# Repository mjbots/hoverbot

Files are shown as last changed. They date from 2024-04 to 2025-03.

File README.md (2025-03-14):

mjbots hoverbot
===============

Source and design files for the mjbots hoverbot, its controlling
interfaces, and utilities for developing and operating it.

* GitHub https://github.com/mjbots/hoverbot
* Most files are free hardware and software: Apache 2.0 License
* F360 assembly: https://a360.co/3Fpwtx1
* [BOM](BOM.md)

Directory structure
-------------------

* **base/** - C++ source files common to many applications.
* **mech/** - C++ source files specific to walking robots.
* **utils/** - Utilities for development and data analysis.
* **configs/** - Configuration files for different robots and applications.
* **hw/** - Hardware design files
* **docs/** - Documentation.

First Time Setup
----------------

The following should work on Ubuntu 22.04

```
./install-packages
```

Building for host
-----------------

```
tools/bazel test //...
```

Building for the target
-----------------------

```
tools/bazel test --config=pi //mech:hoverbot_deploy.tar
```

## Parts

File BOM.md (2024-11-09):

# Hoverbot BOM

* 3D printed parts (all designed for Prusament PETG with a Prusa MK3s and 0.6mm nozzle)
  * [Base](hw/hoverbot_base.3mf)
  * [Chassis](hw/hoverbot_chassis.3mf)
  * [Chassis cover](hw/hoverbot_chassis_cover.3mf)
  * [Base cover, battery rails, and battery cover](hw/hoverbot_rails_base_cover.3mf)
* Electronics
  * 2x [moteus-c1](https://mjbots.com/products/moteus-c1)
  * [pi3hat](https://mjbots.com/products/mjbots-pi3hat-r4-5)
  * [power_dist](https://mjbots.com/products/mjbots-power-dist-r4-5b)
  * [Raspberry Pi 4 / 2GB](https://www.raspberrypi.com/products/raspberry-pi-4-model-b/)
  * [64GB Micro SD Card](https://www.amazon.com/gp/product/B09X7C7LL1)
* Connectors and cabling
  * 3x [30cm PH3 cable](https://mjbots.com/products/jst-ph3-cable)
  * 3x XT30 power cables, each with
    * 1x [XT30 Male](https://mjbots.com/products/xt30u-m)
    * 1x [XT30 Female](https://mjbots.com/products/xt30u-f)
    * ~30cm [18 AWG silicone wire](https://www.amazon.com/gp/product/B01KCPL3Z8)
    * heat shrink tubing
  * 2x motor wiring, each with
    * 1x [MR30 connector pairs](https://www.amazon.com/gp/product/B0747MW9RX)
    * 1x [GH7 housings](https://mjbots.com/products/jst-gh7-housing)
    * 5x [GH pre-crimped wires](https://mjbots.com/products/jst-gh-wire)
    * small heat shrink tubing
  * Power cable
    * [XT90S](https://www.amazon.com/gp/product/B0893CGLP7)
    * ~20cm [16 AWG silicone wire](https://www.amazon.com/gp/product/B01MCRY7OT)
* Battery mount
  * 2x [M3x4 bolt / 91292A109](https://www.mcmaster.com/91292A109/)
  * [Battery PCB](hw/battery_pcb/)
  * 2x [Battery Terminal / 1289](https://www.digikey.com/en/products/detail/keystone-electronics/1289)
* Hardware
  * 28x [M3 heat set inserts / 94180A331](https://www.mcmaster.com/94180A331/)
    * 18x in base
    * 10x in chassis
  * 8x [M2.5 heat set inserts / 94180A321](https://www.mcmaster.com/94180A321/)
    * 8x in chassis
  * 16x [M2.5x5 bolts / 91292A009](https://www.mcmaster.com/91292A009/)
    * 8x for moteus-c1
    * 4x for power_dist
    * 4x for pi3hat
  * 26x [M3x8 bolt 91292A112](https://www.mcmaster.com/91292A112/)
    * 8x for motors
    * 4x for base cover
    * 4x for chassis cover
    * 4x for chassis
    * 6x for battery mounts

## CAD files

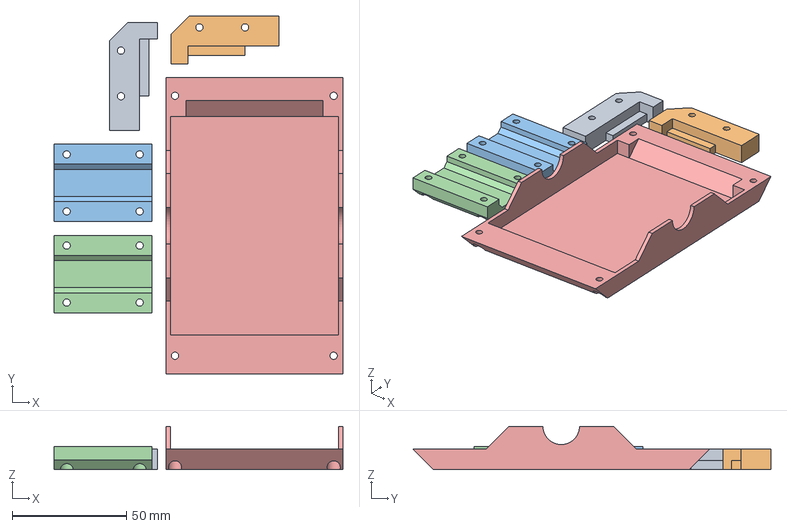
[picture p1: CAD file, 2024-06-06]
hw/hoverbot_rails_base_cover.3mf
126.6 x 157.0 x 19.0 mm
hoverbot_battery_rail2.stl
hoverbot_battery_rail1.stl
hoverbot_motor_mount2.stl
hoverbot_motor_mount1.stl
hoverbot_base_cover.stl

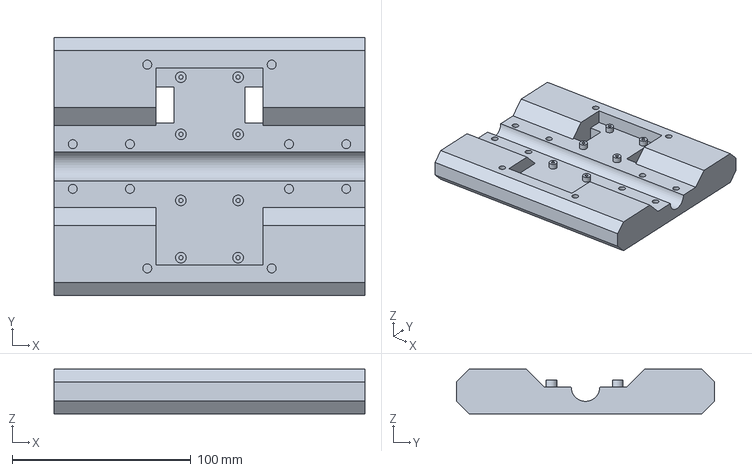
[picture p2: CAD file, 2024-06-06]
hw/hoverbot_base.3mf
174.0 x 144.1 x 25.0 mm

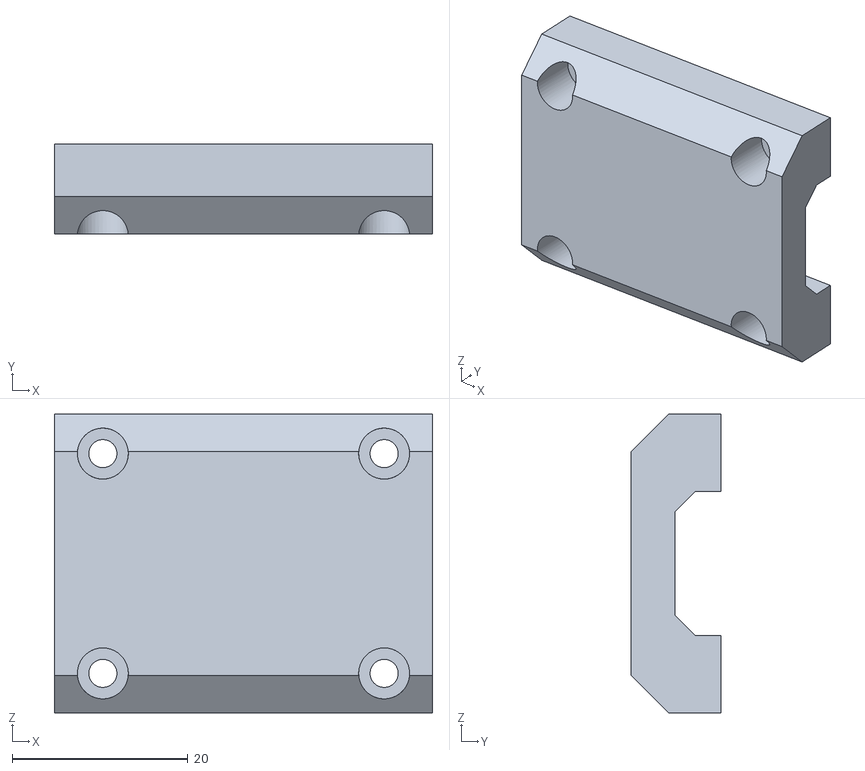
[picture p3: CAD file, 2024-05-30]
hw/hoverbot_motor_mount1.stl
43.0 x 10.2 x 34.0

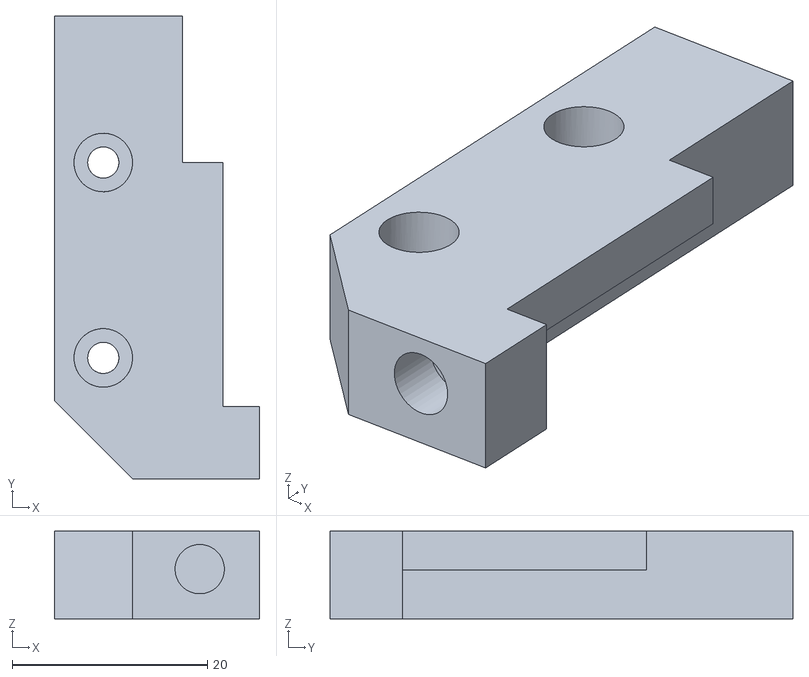
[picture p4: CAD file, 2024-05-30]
hw/hoverbot_battery_rail2.stl
21.0 x 47.4 x 9.00

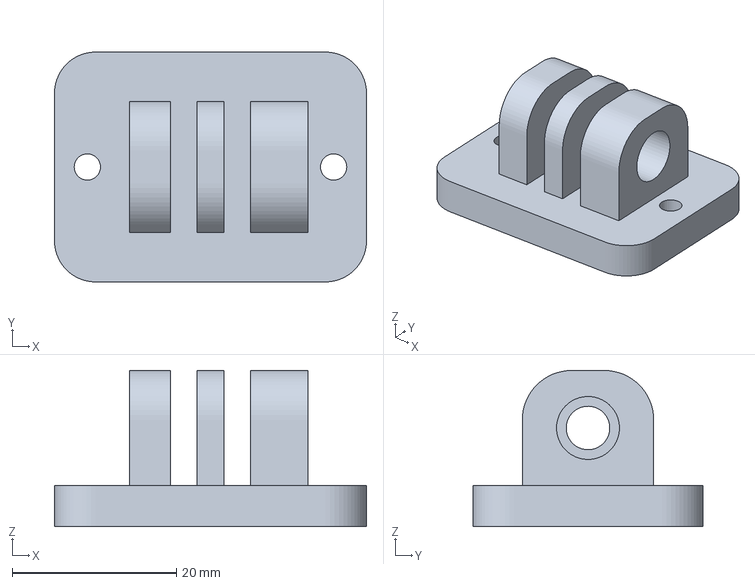
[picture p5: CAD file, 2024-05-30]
hw/gopro_mount.3mf
38.0 x 28.0 x 19.0 mm

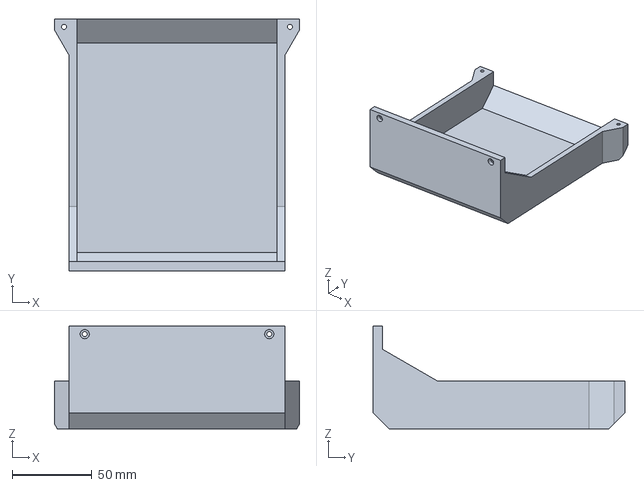
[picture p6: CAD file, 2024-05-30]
hw/hoverbot_chassis_cover.3mf
154.0 x 158.5 x 64.5 mm

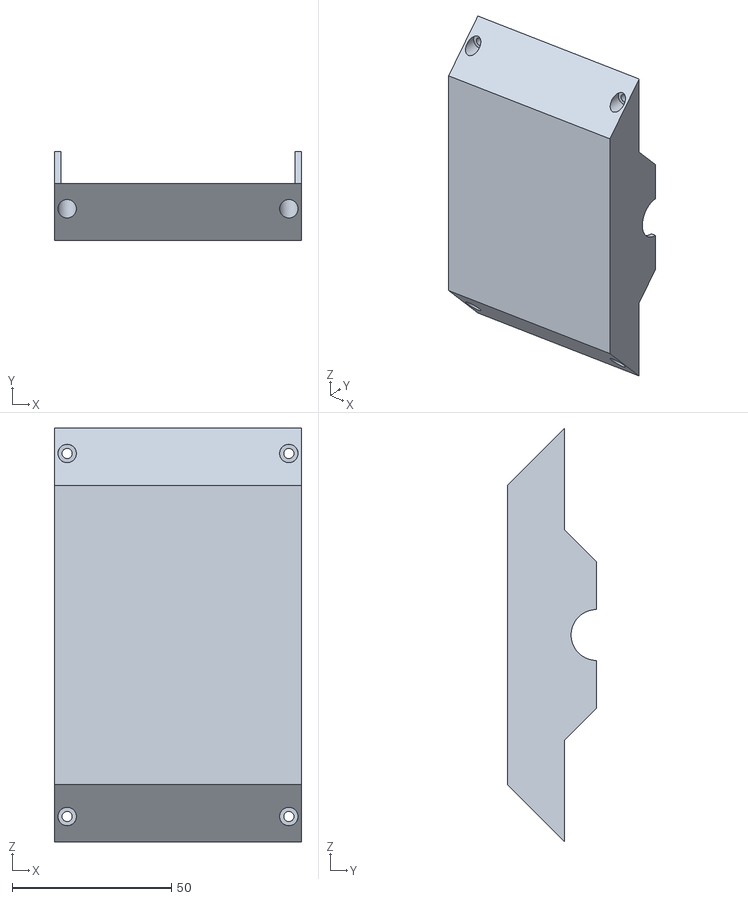
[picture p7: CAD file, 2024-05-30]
hw/hoverbot_base_cover.stl
77.6 x 28.0 x 130.0

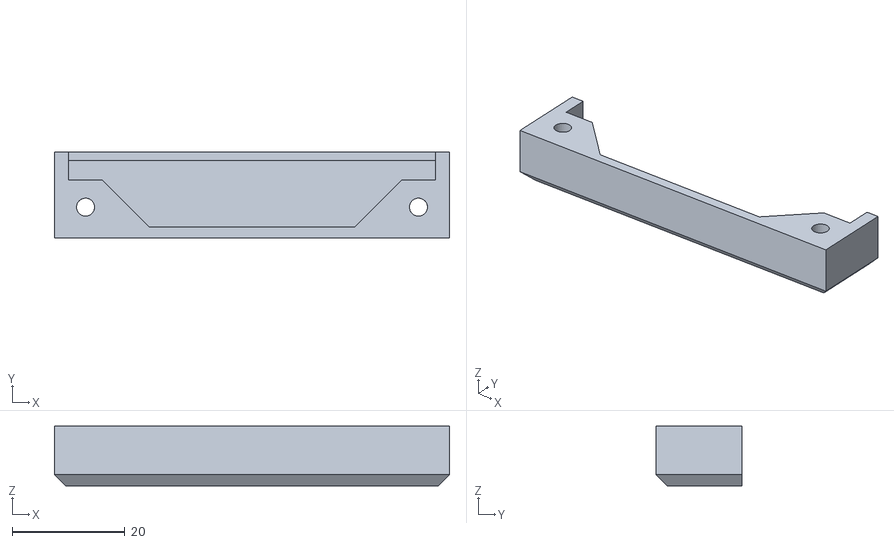
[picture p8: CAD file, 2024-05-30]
hw/hoverbot_battery_cover.stl
70.0 x 15.3 x 10.6

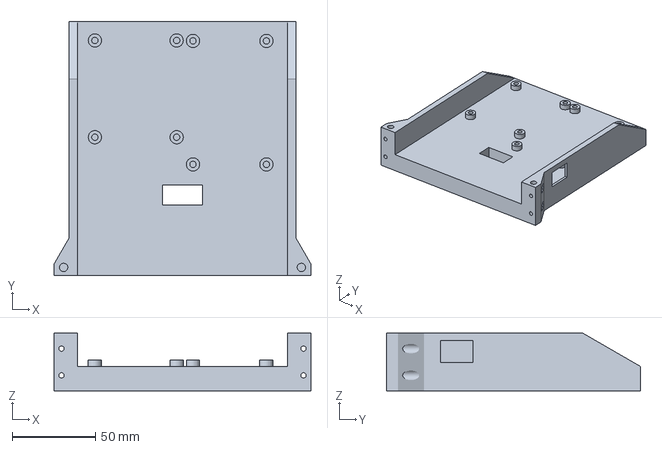
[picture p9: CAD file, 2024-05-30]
hw/hoverbot_chassis.3mf
154.0 x 152.5 x 34.5 mm

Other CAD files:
hw/hoverbot_motor_mount2.stl
hw/hoverbot_battery_rail1.stl
hw/gopro_mount.stl
hw/hoverbot_base.stl
hw/hoverbot_chassis.stl
hw/hoverbot_chassis_cover.stl

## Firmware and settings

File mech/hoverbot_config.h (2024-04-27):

// Copyright 2019-2020 Josh Pieper, jjp@pobox.com.
//
// Licensed under the Apache License, Version 2.0 (the "License");
// you may not use this file except in compliance with the License.
// You may obtain a copy of the License at
//
//     http://www.apache.org/licenses/LICENSE-2.0
//
// Unless required by applicable law or agreed to in writing, software
// distributed under the License is distributed on an "AS IS" BASIS,
// WITHOUT WARRANTIES OR CONDITIONS OF ANY KIND, either express or implied.
// See the License for the specific language governing permissions and
// limitations under the License.

#pragma once

#include <vector>

#include "mjlib/base/pid.h"
#include "mjlib/base/visitor.h"

#include "base/point3d.h"
#include "base/sophus.h"

namespace mjmech {
namespace mech {

// This represents the JSON used to configure the geometry of the
// robot.
struct HoverbotConfig {
  double period_s = 0.0025;
  double min_voltage = 16.0;

  double wheel_diameter_m = 0.163;

  struct Joint {
    int id = 0;
    double sign = 1.0;
    double rezero_pos_deg = 0.0;

    template <typename Archive>
    void Serialize(Archive* a) {
      a->Visit(MJ_NVP(id));
      a->Visit(MJ_NVP(sign));
      a->Visit(MJ_NVP(rezero_pos_deg));
    }
  };

  std::vector<Joint> joints;

  struct StandUp {
    double pitch_rate_dps = 180.0;

    template <typename Archive>
    void Serialize(Archive* a) {
      a->Visit(MJ_NVP(pitch_rate_dps));
    }
  };

  StandUp stand_up;

  struct Pitch {
    double pitch_offset_deg = 0.0;
    mjlib::base::PID::Config pitch_pid;
    mjlib::base::PID::Config yaw_pid;

    template <typename Archive>
    void Serialize(Archive* a) {
      a->Visit(MJ_NVP(pitch_offset_deg));
      a->Visit(MJ_NVP(pitch_pid));
      a->Visit(MJ_NVP(yaw_pid));
    }
  };

  Pitch pitch;

  struct Drive {
    double pitch_limit_deg = 20.0;
    mjlib::base::PID::Config drive_pid;

    template <typename Archive>
    void Serialize(Archive* a) {
      a->Visit(MJ_NVP(pitch_limit_deg));
      a->Visit(MJ_NVP(drive_pid));
    }
  };

  Drive drive;

  double max_tip_deg = 65;
  double tip_filter_s = 0.1;
  double voltage_filter_s = 1.0;

  template <typename Archive>
  void Serialize(Archive* a) {
    a->Visit(MJ_NVP(period_s));
    a->Visit(MJ_NVP(min_voltage));
    a->Visit(MJ_NVP(wheel_diameter_m));
    a->Visit(MJ_NVP(joints));
    a->Visit(MJ_NVP(stand_up));
    a->Visit(MJ_NVP(pitch));
    a->Visit(MJ_NVP(drive));
    a->Visit(MJ_NVP(max_tip_deg));
    a->Visit(MJ_NVP(tip_filter_s));
    a->Visit(MJ_NVP(voltage_filter_s));
  }
};

}
}

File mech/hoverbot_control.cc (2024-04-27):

// Copyright 2019-2020 Josh Pieper, jjp@pobox.com.
//
// Licensed under the Apache License, Version 2.0 (the "License");
// you may not use this file except in compliance with the License.
// You may obtain a copy of the License at
//
//     http://www.apache.org/licenses/LICENSE-2.0
//
// Unless required by applicable law or agreed to in writing, software
// distributed under the License is distributed on an "AS IS" BASIS,
// WITHOUT WARRANTIES OR CONDITIONS OF ANY KIND, either express or implied.
// See the License for the specific language governing permissions and
// limitations under the License.

#include "mech/hoverbot_control.h"

#include <fstream>

#include <boost/algorithm/string.hpp>
#include <boost/asio/post.hpp>

#include <fmt/format.h>

#include "mjlib/base/clipp_archive.h"
#include "mjlib/base/json5_read_archive.h"

#include "mjlib/io/now.h"
#include "mjlib/io/repeating_timer.h"

#include "base/common.h"
#include "base/fit_plane.h"
#include "base/interpolate.h"
#include "base/logging.h"
#include "base/sophus.h"
#include "base/telemetry_registry.h"
#include "base/timestamped_log.h"

#include "mech/attitude_data.h"
#include "mech/moteus.h"
#include "mech/hoverbot_config.h"
#include "mech/hoverbot_context.h"

namespace pl = std::placeholders;

namespace mjmech {
namespace mech {

namespace {
constexpr int kNumServos = 2;

using HC = HoverbotCommand;
using HM = HC::Mode;

template <typename Iter, typename Functor>
auto Average(Iter begin, Iter end, Functor f) -> decltype(f(*begin)) {
  using T = decltype(f(*begin));

  T sum = {};
  double count = {};
  for (Iter it = begin; it != end; ++it) {
    count++;
    sum += f(*it);
  }
  return (1.0 / count) * sum;
}

template <typename Iter, typename Functor>
auto Max(Iter begin, Iter end, Functor f) -> decltype(f(*begin)) {
  using T = decltype(f(*begin));

  MJ_ASSERT(begin != end);

  T current = f(*begin);
  Iter it = begin;
  ++it;
  for (; it != end; ++it) {
    const auto value = f(*it);
    if (value > current) { current = value; }
  }
  return current;
}

template <typename Iter, typename Functor>
auto Min(Iter begin, Iter end, Functor f) -> decltype(f(*begin)) {
  using T = decltype(f(*begin));

  MJ_ASSERT(begin != end);

  T current = f(*begin);
  Iter it = begin;
  ++it;
  for (; it != end; ++it) {
    const auto value = f(*it);
    if (value < current) { current = value; }
  }
  return current;
}

struct ReportedServoConfig {
  boost::posix_time::ptime timestamp;

  struct Servo {
    int id = 0;
    int rezero_state = 0;
    int register_map_version = -1;
    std::array<uint8_t, 12> serial_number = {};

    template <typename Archive>
    void Serialize(Archive* a) {
      a->Visit(MJ_NVP(id));
      a->Visit(MJ_NVP(rezero_state));
      a->Visit(MJ_NVP(register_map_version));
      a->Visit(MJ_NVP(serial_number));
    }
  };

  std::vector<Servo> servos;

  template <typename Archive>
  void Serialize(Archive* a) {
    a->Visit(MJ_NVP(timestamp));
    a->Visit(MJ_NVP(servos));
  }
};

using Config = HoverbotConfig;

struct CommandLog {
  boost::posix_time::ptime timestamp;

  const HC* command = &ignored_command;

  template <typename Archive>
  void Serialize(Archive* a) {
    a->Visit(MJ_NVP(timestamp));
    const_cast<HC*>(command)->Serialize(a);
  }

  static HC ignored_command;
};

HC CommandLog::ignored_command;
}

class HoverbotControl::Impl {
 public:
  Impl(base::Context& context,
       Pi3hatGetter pi3hat_getter)
      : executor_(context.executor),
        telemetry_log_(context.telemetry_log.get()),
        timer_(executor_),
        pi3hat_getter_(pi3hat_getter) {
    context.telemetry_registry->Register("hc_status", &status_signal_);
    context.telemetry_registry->Register("hc_command", &command_signal_);
    context.telemetry_registry->Register("hc_control", &control_signal_);
    context.telemetry_registry->Register("imu", &imu_signal_);
    context.telemetry_registry->Register("servo_config", &servo_config_signal_);
  }

  void AsyncStart(mjlib::io::ErrorCallback callback) {
    pi3hat_ = pi3hat_getter_();

    BOOST_ASSERT(!!pi3hat_);

    // Load our configuration.
    std::vector<std::string> configs;
    boost::split(configs, parameters_.config, boost::is_any_of(" "));
    for (const auto& config : configs) {
      std::ifstream inf(config);
      mjlib::base::system_error::throw_if(
          !inf.is_open(),
          fmt::format("could not open config file '{}'", parameters_.config));

      mjlib::base::Json5ReadArchive(inf).Accept(&config_);
    }

    context_.emplace(config_, &current_command_, &status_.state);

    PopulateStatusRequest();

    period_s_ = config_.period_s;
    rate_hz_ = static_cast<int>(1.0 / config_.period_s);
    timer_.start(mjlib::base::ConvertSecondsToDuration(period_s_),
                 std::bind(&Impl::HandleTimer, this, pl::_1));

    boost::asio::post(
        executor_,
        std::bind(std::move(callback), mjlib::base::error_code()));
  }

  void Command(const HC& command) {
    const auto now = Now();
    const bool higher_priority = command.priority >= current_command_.priority;
    const bool stale =
        !current_command_timestamp_.is_not_a_date_time() &&
        (mjlib::base::ConvertDurationToSeconds(
            now - current_command_timestamp_) > parameters_.command_timeout_s);
    if (!higher_priority && !stale) {
      return;
    }

    CommandLog command_log;
    command_log.timestamp = now;
    command_log.command = &command;

    current_command_ = command;
    current_command_timestamp_ = now;

    // Update our logging status.
    if (command.log != HoverbotCommand::Log::kUnset) {
      if (command.log == HoverbotCommand::Log::kEnable &&
          !telemetry_log_->IsOpen()) {
        base::OpenMaybeTimestampedLog(
            telemetry_log_,
            parameters_.log_filename_base,
            base::kTimestamped);
      } else if (command.log == HoverbotCommand::Log::kDisable &&
                 telemetry_log_->IsOpen()) {
        telemetry_log_->Close();
      }
    }

    command_signal_(&command_log);
  }

  void PopulateStatusRequest() {
    status_request_ = {};

    for (const auto& joint : config_.joints) {
      status_request_.push_back({});
      auto& current = status_request_.back();
      current.id = joint.id;

      // Read mode, position, velocity, and torque.
      current.request.ReadMultiple(moteus::Register::kMode, 4, 1);
      current.request.ReadMultiple(moteus::Register::kVoltage, 3, 0);

      if (parameters_.servo_debug) {
        current.request.ReadMultiple(moteus::Register::kPositionKp, 5, 1);
      }
    }

    config_status_request_ = {};
    for (const auto& joint : config_.joints) {
      config_status_request_.push_back({});
      auto& current = config_status_request_.back();
      current.id = joint.id;
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

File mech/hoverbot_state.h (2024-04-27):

// Copyright 2014-2020 Josh Pieper, jjp@pobox.com.
//
// Licensed under the Apache License, Version 2.0 (the "License");
// you may not use this file except in compliance with the License.
// You may obtain a copy of the License at
//
//     http://www.apache.org/licenses/LICENSE-2.0
//
// Unless required by applicable law or agreed to in writing, software
// distributed under the License is distributed on an "AS IS" BASIS,
// WITHOUT WARRANTIES OR CONDITIONS OF ANY KIND, either express or implied.
// See the License for the specific language governing permissions and
// limitations under the License.

#pragma once

#include <optional>

#include "mjlib/base/pid.h"
#include "mjlib/base/visitor.h"

#include "base/kinematic_relation.h"
#include "base/point3d.h"
#include "base/quaternion.h"

#include "mech/hoverbot_command.h"

namespace mjmech {
namespace mech {

struct HoverbotState {
  // The joint level.
  struct Joint {
    int id = 0;

    // These are the raw values reported by the actuator and are not
    // referenced to any particular frame.
    double angle_deg = 0.0;
    double velocity_dps = 0.0;
    double torque_Nm = 0.0;

    double temperature_C = 0.0;
    double voltage = 0.0;
    int32_t mode = 0;
    int32_t fault = 0;

    double kp_Nm = 0.0;
    double ki_Nm = 0.0;
    double kd_Nm = 0.0;
    double feedforward_Nm = 0.0;
    double command_Nm = 0.0;

    template <typename Archive>
    void Serialize(Archive* a) {
      a->Visit(MJ_NVP(id));
      a->Visit(MJ_NVP(angle_deg));
      a->Visit(MJ_NVP(velocity_dps));
      a->Visit(MJ_NVP(torque_Nm));
      a->Visit(MJ_NVP(temperature_C));
      a->Visit(MJ_NVP(voltage));
      a->Visit(MJ_NVP(mode));
      a->Visit(MJ_NVP(fault));
      a->Visit(MJ_NVP(kp_Nm));
      a->Visit(MJ_NVP(ki_Nm));
      a->Visit(MJ_NVP(kd_Nm));
      a->Visit(MJ_NVP(feedforward_Nm));
      a->Visit(MJ_NVP(command_Nm));
    }
  };

  std::vector<Joint> joints;

  struct StandUp {
    double pitch_target_deg = 0.0;

    template <typename Archive>
    void Serialize(Archive* a) {
      a->Visit(MJ_NVP(pitch_target_deg));
    }
  };

  StandUp stand_up;

  struct Pitch {
    mjlib::base::PID::State pitch_pid;
    mjlib::base::PID::State yaw_pid;
    double yaw_target = 0.0;

    template <typename Archive>
    void Serialize(Archive* a) {
      a->Visit(MJ_NVP(pitch_pid));
      a->Visit(MJ_NVP(yaw_pid));
      a->Visit(MJ_NVP(yaw_target));
    }
  };

  Pitch pitch;

  struct Drive {
    mjlib::base::PID::State drive_pid;

    template <typename Archive>
    void Serialize(Archive* a) {
      a->Visit(MJ_NVP(drive_pid));
    }
  };

  Drive drive;

  // And finally, the robot level.
  struct Robot {
    double velocity_mps = 0.0;
    double accel_mps2 = 0.0;
    double voltage = 0.0;
    double in_control_time_s = 0.0;
    double tip_pitch_deg = 0.0;
    double tip_roll_deg = 0.0;

    template <typename Archive>
    void Serialize(Archive* a) {
      a->Visit(MJ_NVP(velocity_mps));
      a->Visit(MJ_NVP(accel_mps2));
      a->Visit(MJ_NVP(voltage));
      a->Visit(MJ_NVP(in_control_time_s));
      a->Visit(MJ_NVP(tip_pitch_deg));
      a->Visit(MJ_NVP(tip_roll_deg));
    }
  };

  Robot robot;

  template <typename Archive>
  void Serialize(Archive* a) {
    a->Visit(MJ_NVP(joints));
    a->Visit(MJ_NVP(stand_up));
    a->Visit(MJ_NVP(pitch));
    a->Visit(MJ_NVP(drive));
    a->Visit(MJ_NVP(robot));
  }
};

}
}

namespace mjlib {
namespace base {

}
}

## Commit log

2024-04-25 Fork for hoverbot... delete most of the things that are obviously not needed
    [20200223-shoulder.3mf, 20200303-battery_stud.3mf, 20200415-stiffener_left.3mf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]
2024-04-25 Add back in a Joint state
2024-04-25 Make a pass at updating config
    [gimbal_config.txt, hoverbot.cfg, lizard_gimbal_config.txt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]
2024-04-25 Fix compilation on ARM
2024-04-26 Get basic pitch and yaw control working!
    [hoverbot.cfg]
2024-04-26 Basic drive control... doesn't really work that well yet
    [hoverbot.cfg]
2024-04-26 Make it a bit more drivable!
    [hoverbot.cfg]
2024-04-26 Faults now kill power
2024-04-26 Fix the direction of pitch and drive control
    [hoverbot_control.cc]
2024-04-26 Make standing up from laying down work
    [hoverbot.cfg]
2024-04-27 Filter the pitch and roll used for tip detection
2024-05-30 All 3d prints in STL and 3mf form
    [gopro_mount.3mf, gopro_mount.stl, hoverbot_base.3mf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]
2024-05-30 Add link to F360 assembly
2024-06-06 Add a BOM and the battery PCB
    [bosch_pcb-B_Cu.gbr, bosch_pcb-B_Mask.gbr, bosch_pcb-B_Paste.gbr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]
2024-06-06 Try to indent the BOM to render better
